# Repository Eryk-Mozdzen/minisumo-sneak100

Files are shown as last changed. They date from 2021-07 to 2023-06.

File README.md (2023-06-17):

# Autonomous minisumo robot Sneak100 

<p align="center">
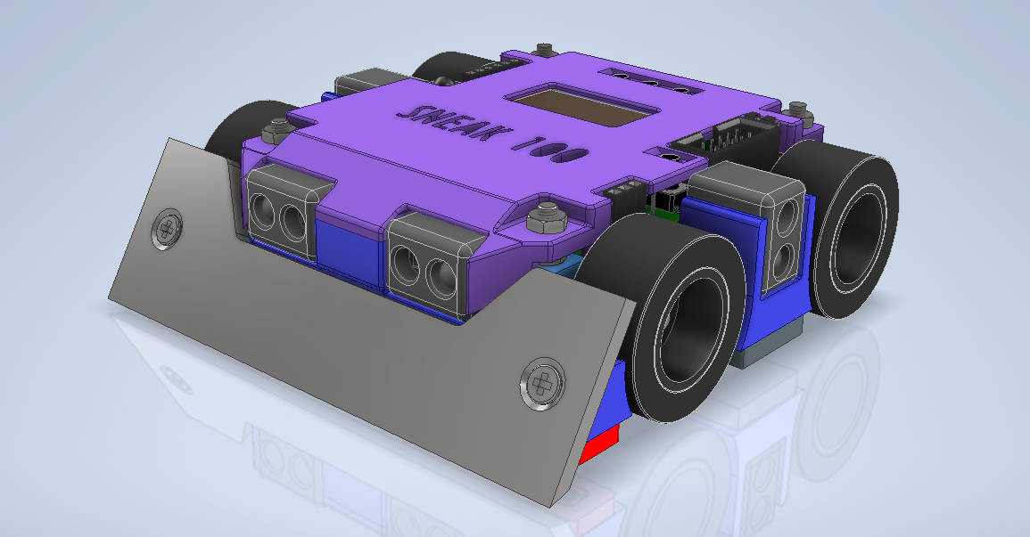
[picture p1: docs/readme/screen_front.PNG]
  
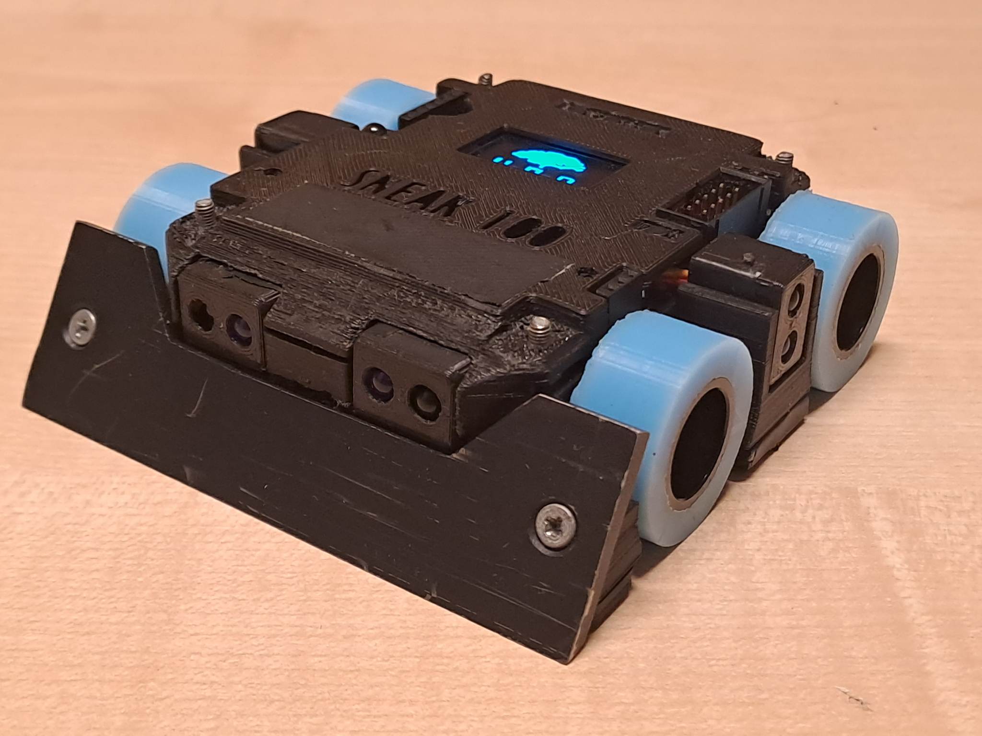
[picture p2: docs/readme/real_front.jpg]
  
</p>

<p align="center">
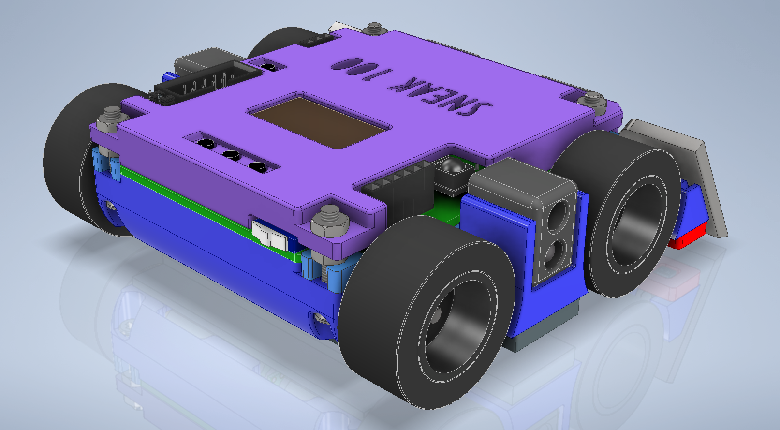
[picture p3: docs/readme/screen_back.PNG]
  
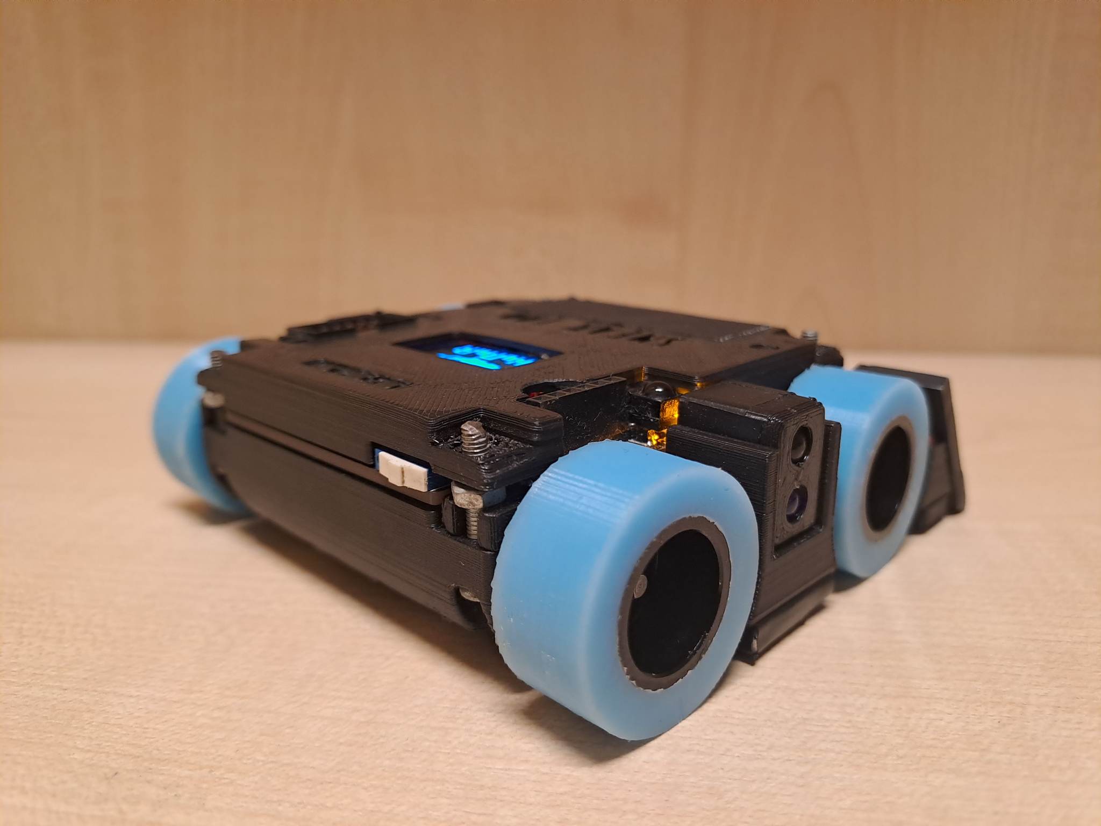
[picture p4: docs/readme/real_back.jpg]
  
</p>

<p align="center">
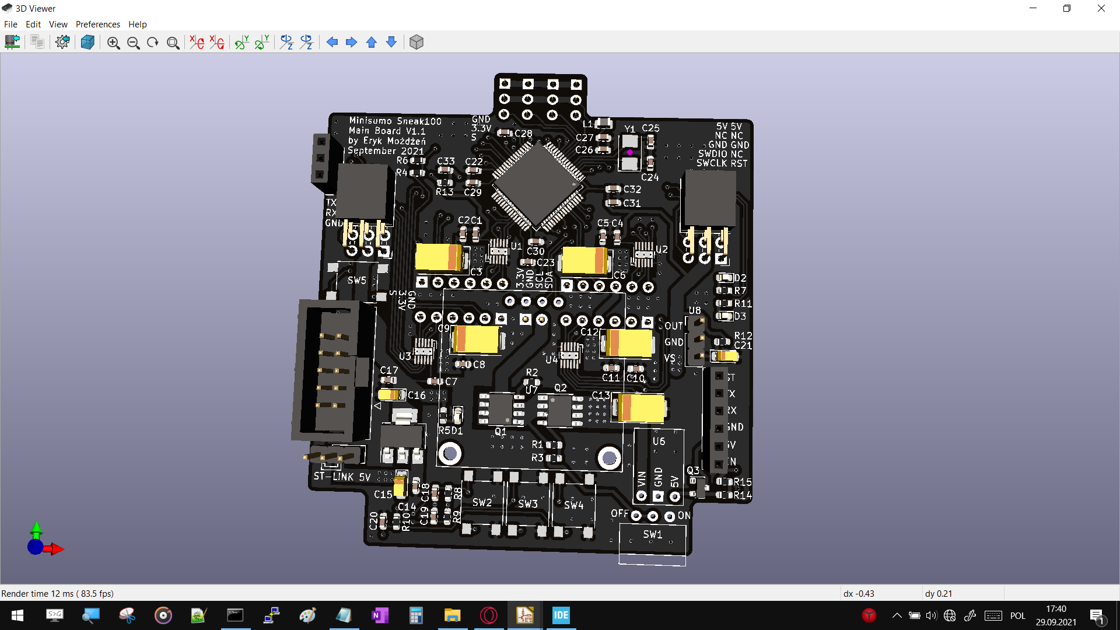
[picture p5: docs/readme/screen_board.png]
  
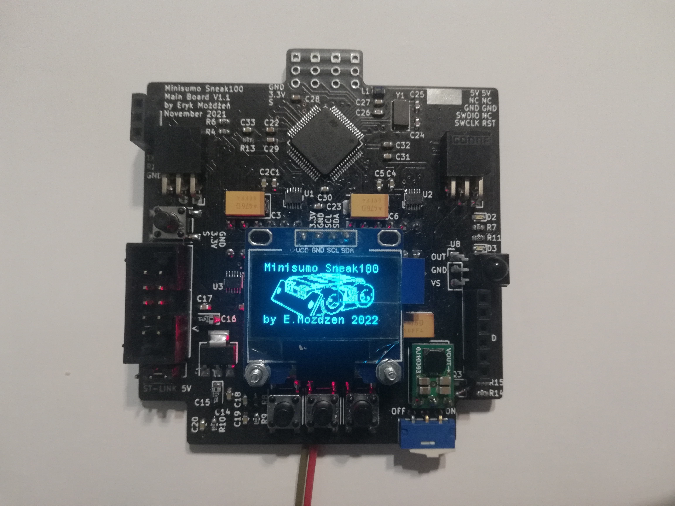
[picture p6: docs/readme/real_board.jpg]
  
</p>

### DEADLINE:
```diff
#  4 sep 2021 - Baltic Robot Battles, Gdansk, Poland (canceled)
- 20 nov 2021 - EastROBO 2021, Bialystok, Poland (missed)
- 28 nov 2021 - ROBOmotion 2021, Rzeszow, Poland (missed)
+  9 apr 2022 - Robotic Tournament, Rybnik, Poland
# 13 may 2022 - Baltic Robot Battles, Gdansk, Poland (canceled)
+ 18 jun 2022 - XIII Robotic Arena, Wroclaw, Poland
-  2 jul 2022 - Drones And Robots Tournament, Krakow, Poland (missed)
+  4 nov 2022 - Robochallnge 2022, Bucharest, Romania
+ 26 nov 2022 - ROBOmotion 2022, Rzeszow, Poland
+  1 apr 2023 - Robotic Tournament, Rybnik, Poland
- 22 apr 2023 - XIV Robotic Arena, Wroclaw, Poland (malfunction)
- 14 may 2023 - Tournoi National de Robotique, Niem, France (malfunction)
```

### Next version:     
- develop spring for blade
- proximity sensors: turn to more front
- hide power switch

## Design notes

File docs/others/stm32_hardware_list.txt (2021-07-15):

proximity sensors:
	- address	3 output
	- tx enable	1 output
	- reflection	1 ADC

line sensors:
	- reflection 	4 ADC

motors:
	- steer		4x2 PWM
	- encoders	4x1 encoder mode

interface:
	- program	SWCLK, SWDIO
	- button	RESET			wycięty
	- user debug	1 UART		zbędny
	- user rc	1 interrupt
	- user button	1 interrupt
	- user leds 	3 output
	
	- IMU		1 SPI/I2C	ok
	- OLED display	1 I2C		ok
	- bluetooth	1 UART		ok
	- start module	2 input		ok	wycięty
	- debug/program	1 USB		ok

others:
	- battery	1 ADC		ok

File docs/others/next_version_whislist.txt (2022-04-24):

version 1.1:
ok	- MOSFET symbol fix
ok	- display mounting holes
ok	- ST-link 5V jumper with 3 pins
ok	- power switch on/off silk layer text
ok	- power led indicator in other place
pass	- swap RC-5 receiver, decoder & state machine to external start module

ok?	- add HC-05 module power control MOSFET
ok	- better STM32 pin usage
ok	- add additional UART
ok	- reset button

version 1.2:
version 2.0:
	- capacitor footprint termo relief
ok	- change polarity of battery input connector to flat side
	- fix proximity sensor connector pinout and add pinout labels / move sensor on the board
ok	- line sensor merged header
ok	- remove HC-05 power control MOSFET / remove HC-05
ok	- add jumper from ST-Link 5V to supply or 5V rail
	- add KoNaR symbol on silk layer
	
	- detachable screen
pass	- detachable 9DOF / 9DOF onboard / 6DOF + 3DOF on board

pass	- use SWO interface for debug, use of real ST-LINK v2, change programming connector to header goldpin

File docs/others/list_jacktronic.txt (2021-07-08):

1	STM32F405RTG6				45	45
6	DRV8835DSSR				5,50	33
5	CD4051 SMD SOP16			1	5
1	Kwarc 8.000 MHz 5x3,2mm 2PAD SMD	3	3
3	Dioda nad.3mm OSIXCA3131A		1,80	5,40
2	Gniazdo USB-mini B smd CANON		2	4

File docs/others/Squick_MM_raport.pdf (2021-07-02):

Projekt

Roboty Mobilne

# Dokumentacja

# Robot mobilny typu MicroMouse

# „Squick”

Skład grupy:
Piotr Gorzelnik, 248947
Patryk Szydlik, 248949

Termin: środa 18:00

Prowadzący:
mgr inż. Arkadiusz Mielczarek

1 lipca 2021

## Spis treści

1 Opis projektu | 2
2 Założenia Projektowe | 2
3 Konfiguracja mikrokontrolera | 3
4 Urządzenia zewnętrzne | 8
5 Projekt elektroniki | 10
6 Konstrukcja mechaniczna | 11
7 Opis działania programu | 14
8 Napotkane problemy | 20
9 Zadania niezrealizowane | 20
10 Podsumowanie | 21
11 Odnośniki do repozytorium GIT Bitbucket | 21

## 1 Opis projektu

Tworzonym przez nas projektem jest robot mobilny klasy micromouse. Będzie on wyposażony w dwukołowy napęd różnicowy (robot mobilny klasy 2.0). Robot będzie korzystał z fuzji czujników odbiciowych time-of-flight oraz czujników stworzonych z nadajników IR oraz fototranzystorów w celu optymalnego rozpoznawania przeszkód (ścian labiryntu). Do orientacji w labiryncie robot będzie wykorzystywać enkodery oraz IMU. Oprócz trybu autonomicznego, robotem będzie także można sterować zdalnie przy użyciu prostej aplikacji mobilnej. Projekt planujemy w przyszłości wykorzystać do wystartowania w zawodach robotycznych. Założenia konstrukcyjne oraz funkcjonalność robota zostały stworzone w oparciu o regulamin konkurencji Micromouse 16x16 odbywającej się na międzynarodowych zawodach robotycznych Robotic Arena.

## 2 Założenia Projektowe

- Użycie mikrokontrolera z rodziny STM32F4
- Stworzenie fuzji dalmierzy laserowych VL oraz ręcznie robionych czujników
- Wykorzystanie enkoderów oraz regulatora PID do sterowania prędkościami silników
- Wykorzystanie IMU oraz modułu Bluetooth
- Pozycjonowanie się w centrum korytarza labiryntu przez regulator PID z czujników odległości
- Obsługa interfejsów komunikacyjnych I2C, SPI, UART
- Konstrukcja mieszcząca się w kwadracie o boku 100mm
- Nisko położony środek ciężkości

### 2.1 Elementy do stworzenia konstrukcji robota

- Mikrokontroler STM32F411RET6 w obudowie LQFP 64 (https://kamami.pl/stm32f4/233364-stm32f411ret6.html?search_query=STM32F4&results=100)
- Czujnik odległości time of flight VL53L0X (https://botland.com.pl/czujniki-swiatla-i-koloru/7176-vl53l0x-time-of-flight-czujnik-odleglosci-i-swiatla-otoczenia-i2c-pololu-2490.html)
- Enkodery magnetyczne do silników pololu micro (https://botland.com.pl/enkodery/4884-zestaw-enkoderow-magnetycznych-do-micro-silnikow-pololu-kompatybilne-z-hpcb-27-18v-2-szt-pololu-3081.html)
- Silniki Pololi HPCB 50:1 z obustronnym wałem (https://botland.com.pl/silniki-dc-micro-z-przekladnia/5093-silnik-hpcb-501-obustronny-wal-pololu-3073.html)
- Moduł komunikacji BT (https://botland.com.pl/moduly-bluetooth/9515-modul-bluetooth-40-ble-hm-10-mlt-bt05-33v5v.html)
- LSM9DS1 - 9DoF IMU - 3-osiowy akcelerometr, magnetometr i żyroskop (https://botland.com.pl/czujniki-9dof-imu/17201-lsm9ds1-9dof-imu-3-osiowy-akcelerometr-magnetometr-i-zyroskop-i2cspi-adafruit-4634.html)
- Nadajniki IR (https://botland.com.pl/diody-ir-podczerwone/279-nadajnik-ir-sfh4550-5mm-850nm.html) oraz Fototranzystory (https://botland.com.pl/fototranzystory/4245-fototranzystor-sfh-313fa-5mm-870nm-5-szt.html)
- Dodatkowe przyciski i przełączniki dla użytkownika
- Diody LED do sygnalizacji
- Multiplekser (http://electropark.pl/4xxx/11374-cd4051-multiplexer-demultiplexer-so16.html)

### 2.2 Możliwości rozwoju konstrukcji w przyszłości

- Wykorzystanie systemu FreeRToS
- Opracowanie filtr Kalmana z IMU
- Wykorzystanie MicroPython-a na mikrokontrolerze
- Wykorzystanie w pełni możliwości FPU na STM32F4
- Rozwinięcie algorytmów eksploracji labirytnu
- Rozwinięcie algorytmów odnajdywania najkrótszej ścieżki

## 3 Konfiguracja mikrokontrolera

Do projektu wybrano mikrokontroler STM32F411RET6 w obudowie LQFP64. Wybór podyktowany został tym, że posiada on wystarczającą moc obliczeniową, ilość potrzebnych peryferiów oraz pamieć flash. Dodatkowo ważnym aspektem była kompatybilność mikrokontrolera z systemami FreeRTOS oraz MicroPython.Na zdjęciu poniżej umieszczono wstępną konfigurację pinów kontrolera, ostateczna struktura może ulec zmianie.

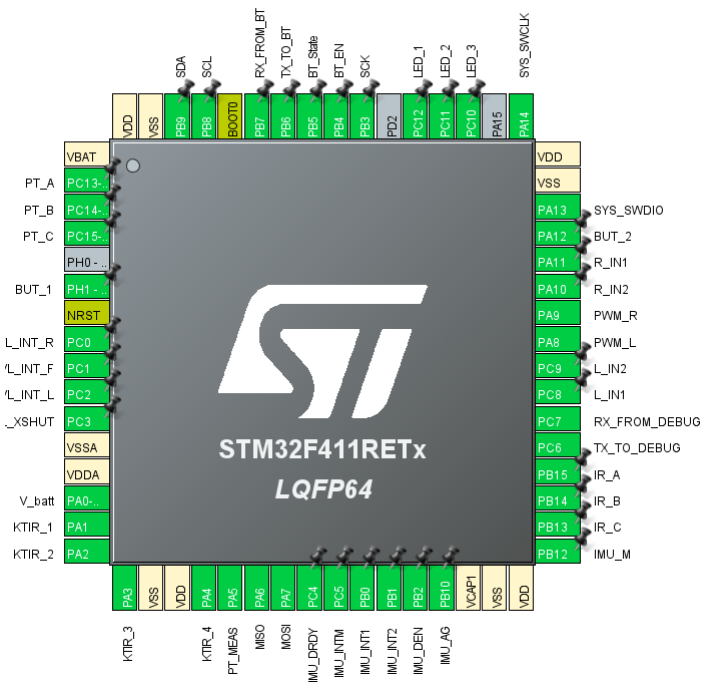
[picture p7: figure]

Rysunek 1: Konfiguracja wyjść mikrokontrolera w programie STM32CubeMX

Rysunek 2: Konfiguracja zegarów mikrokontrolera

### 3.1 Konfiguracja pinów

Numer pinu | PIN | Tryb pracy | Funkcja/etykieta
2 | PC13 | GPIO_Output | PT_A
3 | PC14 | GPIO_Output | PT_B
4 | PC15 | GPIO_Output | PT_C
6 | PH1 | GPIO_Input | BUT_1
8 | PC0 | GPIO_EXTI0 | VL_INT_R
9 | PC1 | GPIO_EXTI1 | VL_INT_F
10 | PC2 | GPIO_EXTI2 | VL_INT_L
11 | PC3 | GPIO_Output | VL_XSHUT
14 | PA0 | ADC1_IN0 | V_batt
15 | PA1 | ADC1_IN1 | KTIR_1
16 | PA2 | ADC1_IN2 | KTIR_2
17 | PA3 | ADC1_IN3 | KTIR_3
20 | PA4 | ADC1_IN4 | KTIR_4
21 | PA5 | ADC1_IN5 | PT_MEAS
22 | PA6 | SPI1_MISO | MISO
23 | PA7 | SPI1_MOSI | MOSI
24 | PC4 | GPIO_Input | IMU_DDRDY
25 | PC5 | GPIO_Input | IMU_INTM
26 | PB0 | GPIO_Input | IMU_INT1
27 | PB1 | GPIO_Input | IMU_INT2
28 | PB2 | GPIO_Output | IMU_DEN
29 | PB10 | GPIO_Output | IMU_AG
33 | PB12 | GPIO_Output | IMU_M
34 | PB13 | GPIO_Output | IR_C
35 | PB14 | GPIO_Output | IR_B
36 | PB15 | GPIO_Output | IR_A
37 | PC6 | USART6_TX | TX_TO_DEBUG
38 | PC7 | USART6_RX | RX_FROM_DEBUG
39 | PC8 | GPIO_Output | L_IN1
40 | PC9 | GPIO_Output | L_IN2
41 | PA8 | TIM1_CH1 (PWM) | PWM_L
42 | PA9 | TIM1_CH2 (PWM) | PWM_R
43 | PA10 | GPIO_Output | R_IN2
44 | PA11 | GPIO_Output | R_IN1
45 | PA12 | GPIO_Input | BUT_2
46 | PA13 | SYS_SWDIO | SYS_SWDIO
49 | PA14 | SYS_SWCLK | SYS_SWCLK
51 | PC10 | GPIO_Output | LED_3
52 | PC11 | GPIO_Output | LED_2
53 | PC12 | GPIO_Output | LED_1
55 | PB3 | SPI1_SCK | SCK
56 | PB4 | GPIO_Output | BT_EN
57 | PB5 | GPIO_Input | BT_State
58 | PB6 | USART1_TX | TX_TO_BT
59 | PB7 | USART1_RX | RX_FROM_BT
61 | PB8 | I2C1_SCL | SCL
62 | PB8 | I2C1_SDA | SDA

Tabela 1: Konfiguracja pinów mikrokontrolera

### 3.2 USART1

Wykorzystany do komunikacji z modułem Bluetooth.

Parametr | Wartość
Baud Rate | 11520
Word Length | 8 Bits (including parity)
Parity | None
Stop Bits | 1
Data Direction | Receive and Transmit
Over sampling | 16 Samples

Tabela 2: Konfiguracja peryferium USART1

### 3.3 USART6

Dodatkowy interfejs UART do komunikacji z osobnym debugerem.

Parametr | Wartość
Baud Rate | 11520
Word Length | 8 Bits (including parity)
Parity | None
Stop Bits | 1
Data Direction | Receive and Transmit
Over sampling | 16 Samples

Tabela 3: Konfiguracja peryferium USART6

### 3.4 I2C1

Interfejs I2C do komunikacji z czujnikami VL

Parametr | Wartość
I2C Speed Mode | Standard Mode
I2C Clock Speed (Hz) | 100 000
Clock No Stretch Mode | Disabled
Primary Address Length selection | 7-bit
Dual Address Acknowledged | Disabled
Primary Slave Address | 0
General Call Address detection | Disabled

Tabela 4: Konfiguracja peryferium I2C1

### 3.5 SPI1

Interfejs SPI do komunikacji z czujnikiem IMU (akcelerometr, żyroskop, magnetometr)

Parametr | Wartość
Frame Format | Motorola
Data Size | 8 Bits
First Bit | MSB First
Prescaler | 16
Baud Rate | 3 MBits/s
Clock Polarity | Low
Clock Phase | 1 Edge
CRC Calculation | Disabled
NSS Signal Type | Software

Tabela 5: Konfiguracja peryferium SPI1

### 3.6 TIM1

To peryferium jest wykorzystywane do zadawania sygnału PWM na silniki

Parametr | Wartość
I2C Speed Mode | Standard Mode
Prescaler | 4
Counter Mode | Up
Counter Period | 999
Internal Clock Division | No Division
Master/Slave Mode | Disable (Trigger input effect not delayed)
Trigger Event Selection | Reset (UG bit from TIMx_EGR)
PWM Generation Channel 1:
Mode | PWM mode1
Pulse | 0
Fast Mode | Disable
CH Polarity | High
PWM Generation Channel 2:
Mode | PWM mode1
Pulse | 0
Fast Mode | Disable
CH Polarity | High

Tabela 6: Konfiguracja peryferium TIM1

### 3.7 TIM2

Ten Timer służy do wywoływania przerwań z częstotliwością 50Hz

Parametr | Wartość
I2C Speed Mode | Standard Mode
Prescaler | 96
Counter Mode | Up
Counter Period | 9999
Internal Clock Division | No Division
Auto-reload Preload | No Disable
Master/Slave Mode | Disable (Trigger input effect not delayed)
Trigger Event Selection | Reset (UG bit from TIMx_EGR)

Tabela 7: Konfiguracja peryferium TIM2

## 4 Urządzenia zewnętrzne

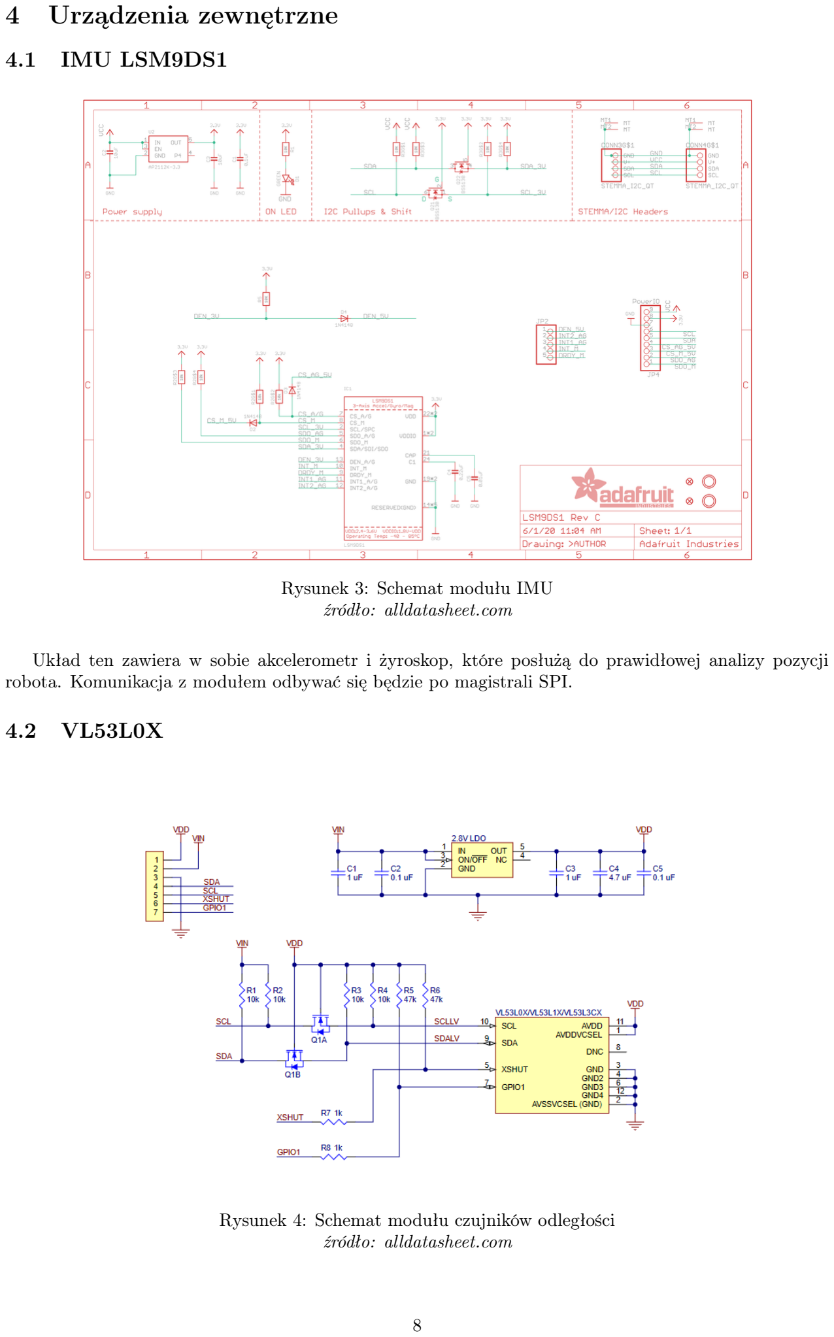
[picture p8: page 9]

### 4.1 IMU LSM9DS1

Rysunek 3: Schemat modułu IMU źródło: alldatasheet.com (https://html.alldatasheet.com/html-pdf/1242998/STMICROELECTRONICS/LSM9DS1/2267/1/LSM9DS1.html)

Układ ten zawiera w sobie akcelerometr i żyroskop, które posłużą do prawidłowej analizy pozycji robota. Komunikacja z modułem odbywać się będzie po magistrali SPI.

### 4.2 VL53L0X

Rysunek 4: Schemat modułu czujników odległości źródło: alldatasheet.com (https://html.alldatasheet.com/html-pdf/948120/STMICROELECTRONICS/VL53L0X/1944/1/VL53L0X.html)

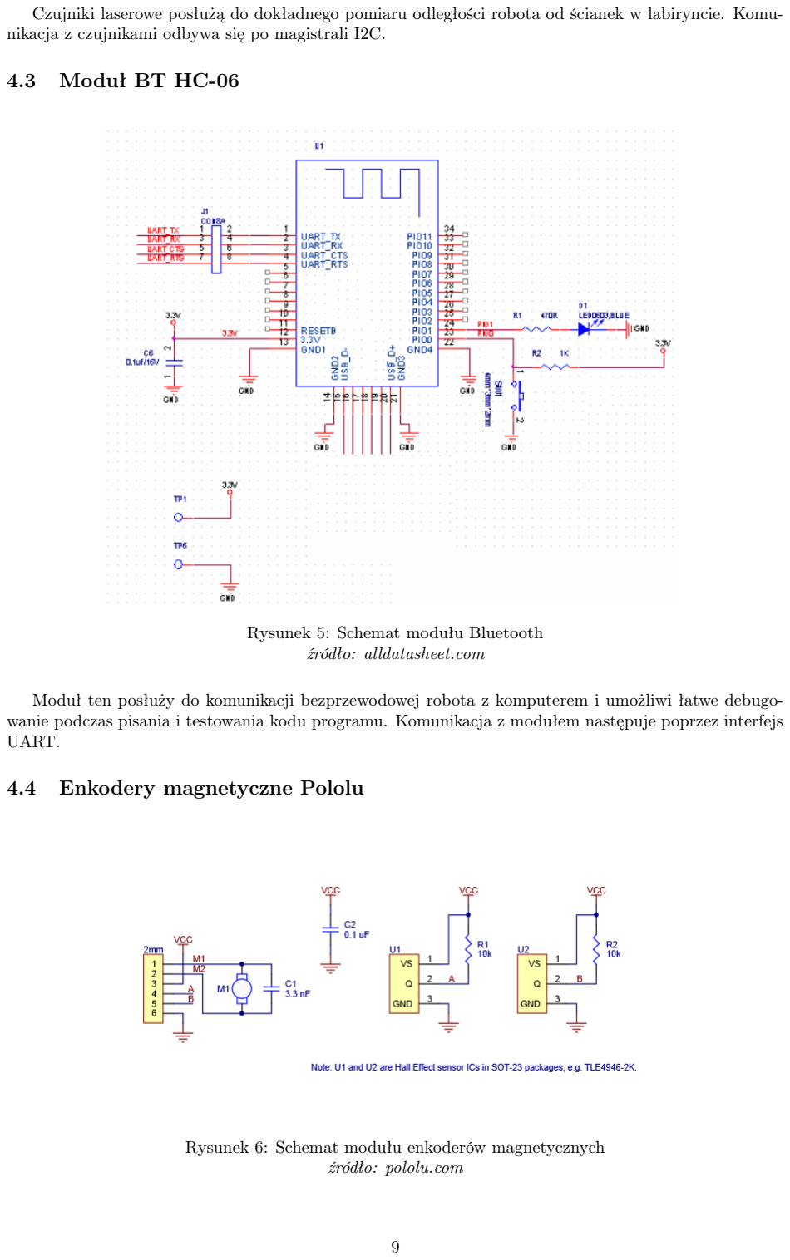
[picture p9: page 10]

Czujniki laserowe posłużą do dokładnego pomiaru odległości robota od ścianek w labiryncie. Komunikacja z czujnikami odbywa się po magistrali I2C.

### 4.3 Moduł BT HC-06

Rysunek 5: Schemat modułu Bluetooth źródło: alldatasheet.com (https://pdf1.alldatasheet.com/datasheet-pdf/view/1179032/ETC1/HC-06.html)

Moduł ten posłuży do komunikacji bezprzewodowej robota z komputerem i umożliwi łatwe debugowanie podczas pisania i testowania kodu programu. Komunikacja z modułem następuje poprzez interfejs UART.

### 4.4 Enkodery magnetyczne Pololu

Rysunek 6: Schemat modułu enkoderów magnetycznych źródło: pololu.com (https://www.pololu.com/file/download/magnetic-encoder-kit-for-micro-metal-gearmotors-schematic.pdf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)

Enkodery magnetyczne wykorzystane zostaną do pomiaru prędkości oraz pozycji obrotowej kół. Zamocowane są one do przedłużonego wału silnika Pololu HCPCB.

## 5 Projekt elektroniki

Schemat całej elektroniki robota znajduje się w załączniku do tego raportu (str. 21). Zarówno schemat elektroniki jak i projekt PCB wykonaliśmy w programie KiCad. Ponieważ płytka drukowana będzie jednocześnie pełnić rolę podwozia, staraliśmy się w miarę możliwości zrobić ją jak najmniejszą, aby zmaksymalizować manewrowalność robota w labiryncie. Z tego też powodu płytka jest dwuwarstwowa.

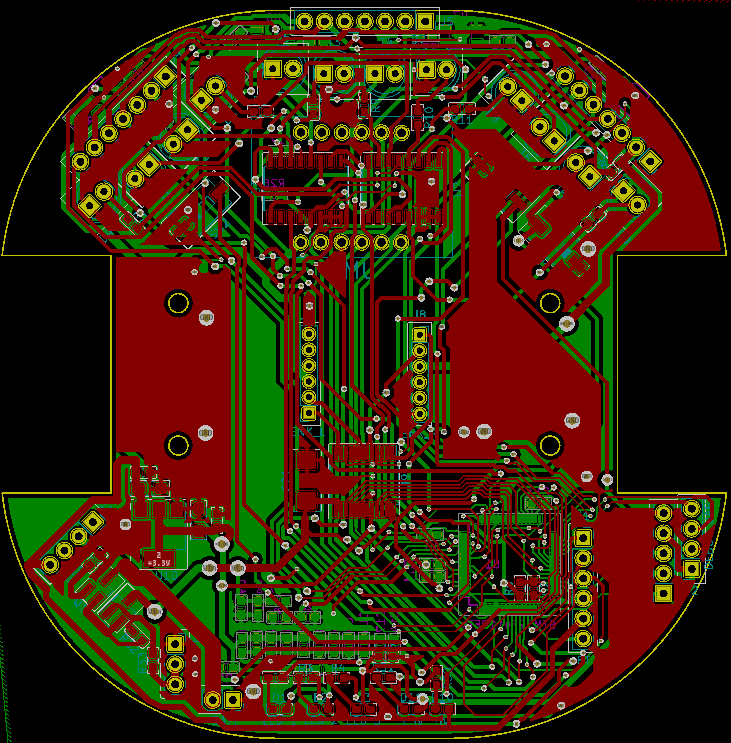
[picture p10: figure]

((a)) Górna warstwa płytki | ((b)) Dolna warstwa płytki

Zdecydowaliśmy się zlecić produkcję płytki w zewnętrznej firmie, aby uniknąć niedoskonałości jakie powstają przy ręcznym wytrawianiu a budżet pozwalał nam na taką wygodę. Zamówienie już do nas dotarło i przewidujemy, że do końca kwietnia ukończymy konstrukcję robota. Poniżej znajdują się zdjęcia gotowych, niepolutowanych płytek.

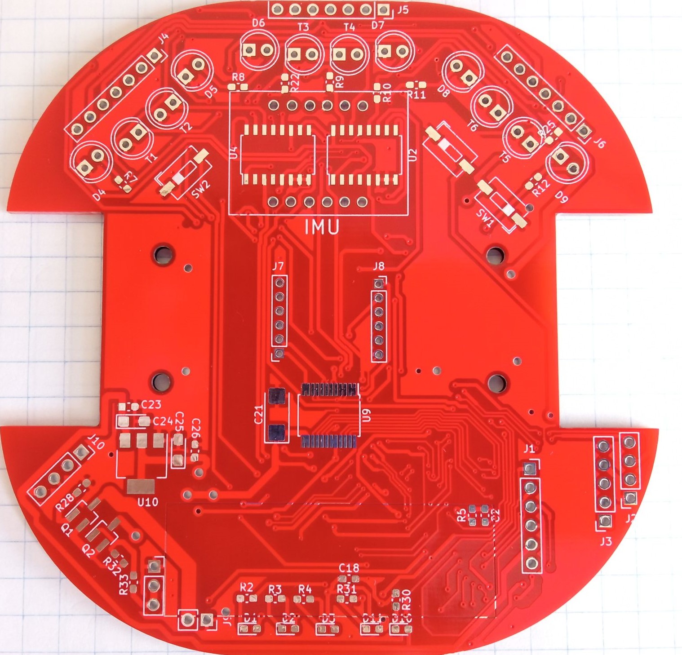
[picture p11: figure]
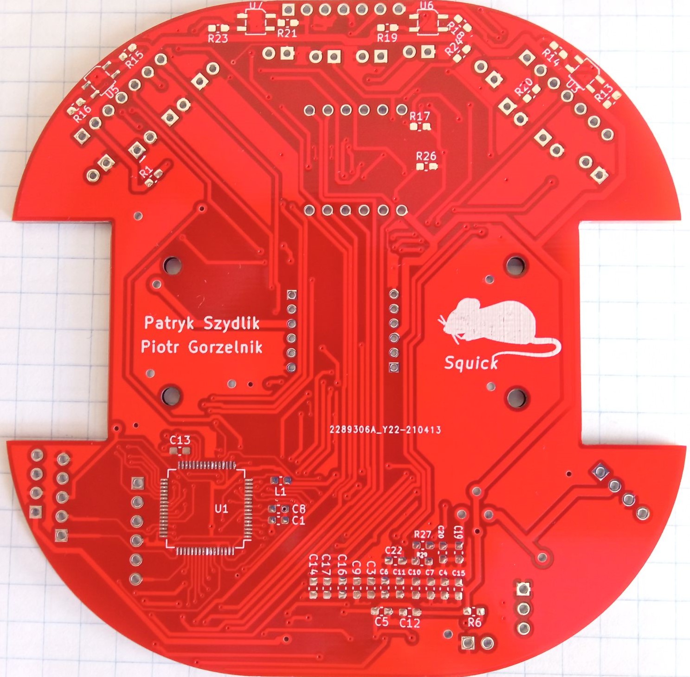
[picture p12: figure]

((a)) Górna warstwa płytki | ((b)) Dolna warstwa płytki

## 6 Konstrukcja mechaniczna

### 6.1 Model 3D

Trójwymiarowy model robota powstał w programie AutoCAD Inventor.

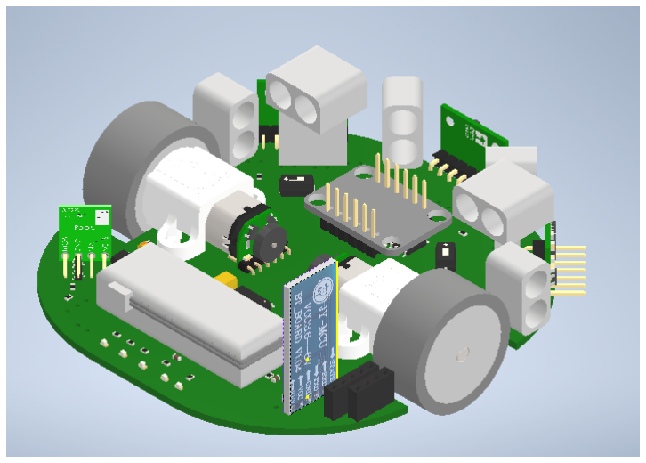
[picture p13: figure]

Rysunek 7: Model konstrukcji robota

Rysunek 8: Rzut z góry modelu robota

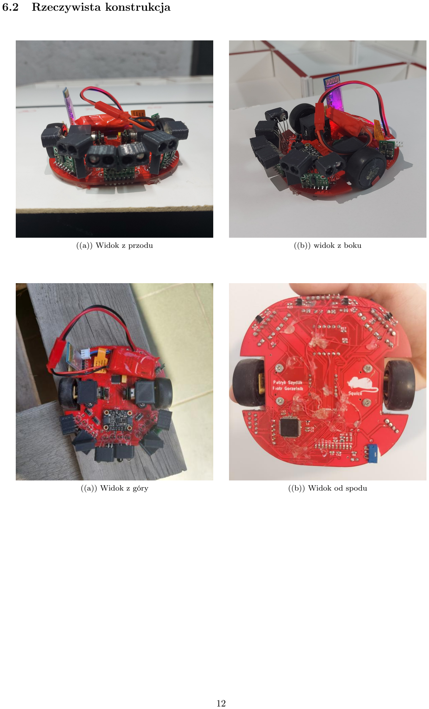
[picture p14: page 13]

### 6.2 Rzeczywista konstrukcja

((a)) Widok z przodu | ((b)) widok z boku
((a)) Widok z góry | ((b)) Widok od spodu

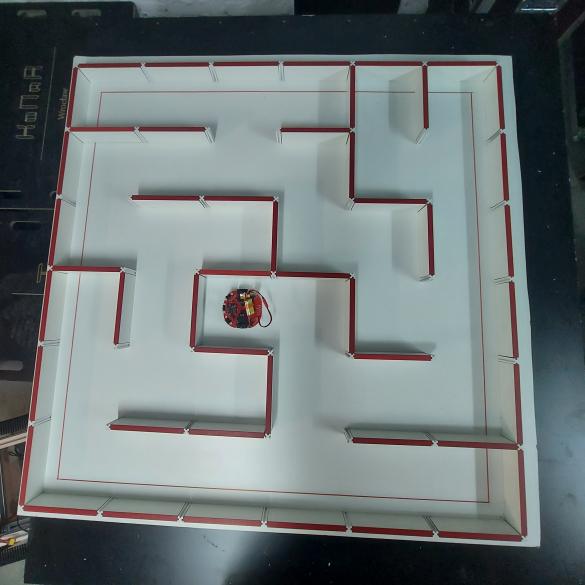
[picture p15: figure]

Rysunek 9: Robot w labiryncie

Jak widać na powyższych zdjęciach, zgodnie z początkowymi założeniami udało nam się stworzyć konstrukcję robota o rozmiarach i kształcie pozwalających na swobodne poruszanie się wewnątrz labiryntu.

## 7 Opis działania programu

### 7.1 Rdzeń programu

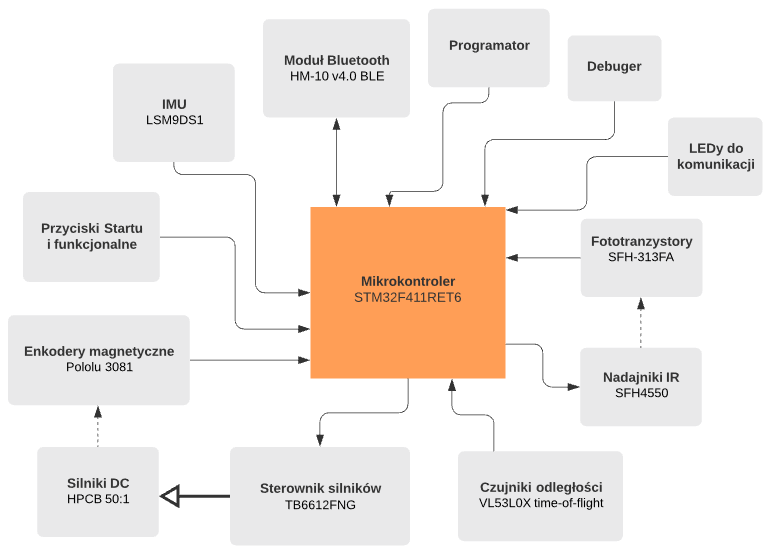
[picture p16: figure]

Rysunek 10: Diagram blokowy rdzenia programu

### 7.2 Obsługa czujników i sterowników

### 7.2.1 Obsługa enkoderów

Po podłączeniu prawidłowym enkoderów Pololu oraz dodatkowym skonfigurowaniu wyjść TIM3 CH1 CH2 oraz TIM2 CH1 CH2 jako encoder mode możliwy był odczyt impulsów odbieranych przez enkodery, a następnie prawidłowa ich konwersja na jednostki odległości mierzone w mm.

Pierwszym ważnym etapem konwersji było skalibrowanie pomiarów z enkoderów oraz ich prawidłowa konwersja:

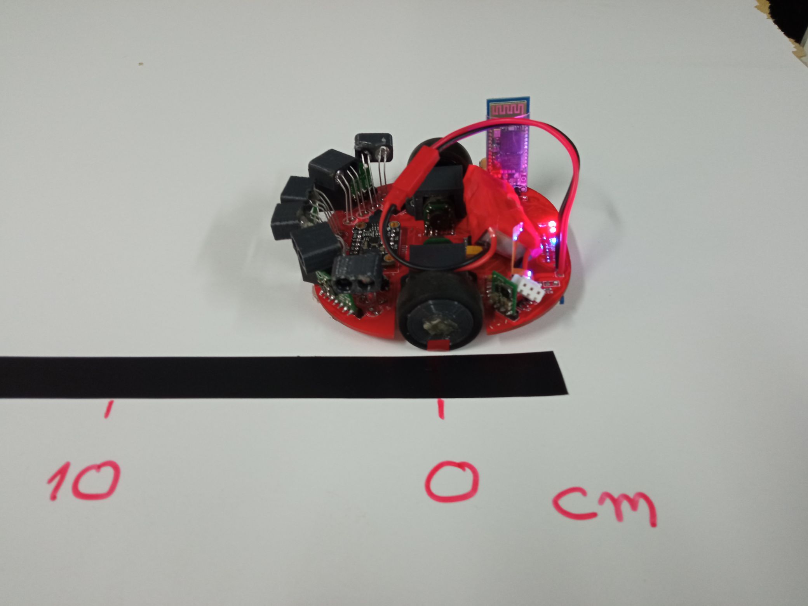
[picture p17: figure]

((a)) Pozycja startowa | ((b)) Wartości odczytów z enkoderów

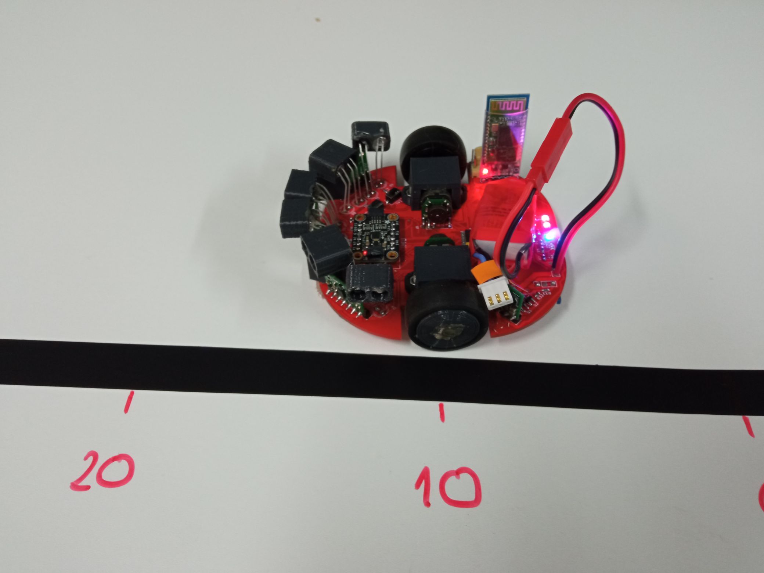
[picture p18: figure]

((a)) Pozycja po przesunięciu o 10cm | ((b)) Odczyty po przesunieciu

Kolejną istotną kwestią po skalibrowaniu odczytów pozycji robota ważne było aby prawidłowo przekształcać i wykorzystywać odczyty z prędkości. W tym celu wykonany był kolejny odpowiedni pomiar, w którym robot przejeżdżał przez sekundę po torze z zadanym wypełnieniem PWM oraz co 100ms wyświetlał pozycję i prędkość.

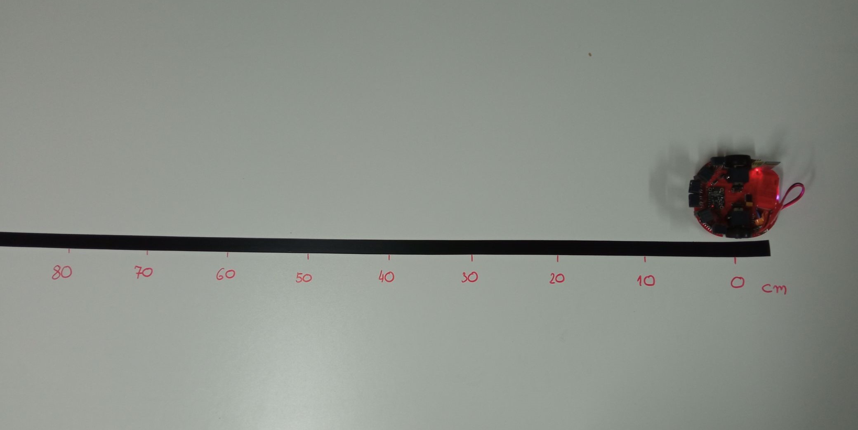
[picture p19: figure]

Rysunek 11: Pozycja startowa na torze

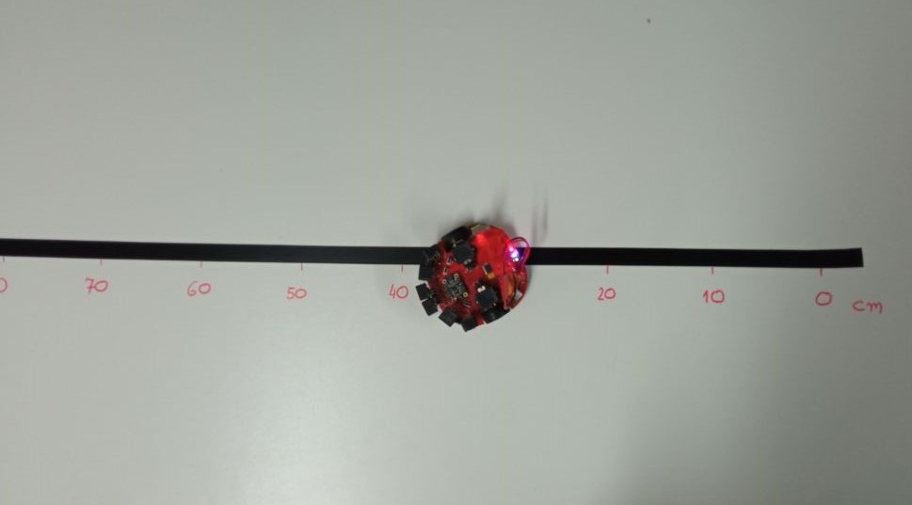
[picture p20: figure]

Rysunek 12: Pozycja końcowa na torze

Rysunek 13: Odczyt z kalibracji

### 7.2.2 Kalibracja PID kontrolującego silniki

Po prawidłowym obsłużeniu odczytów z enkoderów możliwe było napisanie regulatora PID i ręczne jego nastrojenie.
Na poniższych screenach SET oznacza wartość oczekiwaną, MEAS jest wartością zmierzoną na enkoderach, RES to poprawka regulacji PWM wysłanego na silniki.

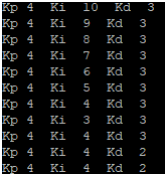
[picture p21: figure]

Rysunek 14: Strojenie PID

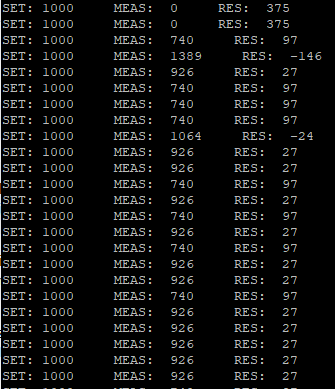
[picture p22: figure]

Rysunek 15: Start regulacji

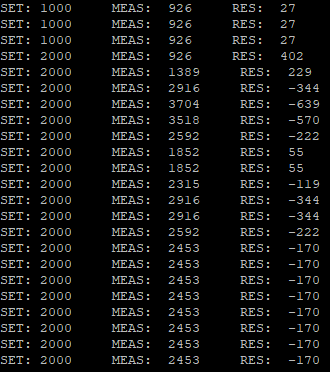
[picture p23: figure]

Rysunek 16: Zmiana set point

Rysunek 17: Wyzerowanie set point

### 7.2.3 Obsługa pomiarów ADC

Odczyty ADC posłużyły m.in do pomiaru i pilnowania stanu napięcia na baterii jak również do oczytów z czujników KTIR, które służą do wykrywania linii na torze.
Niestety jeden z czujników KTIR nadal nie działał. Najprawdopodobniej uszkodzeniu mogły ulec ścieżki prowadzące do tegoż czujnika i nie odbieraliśmy z niego żadnych sygnałów.

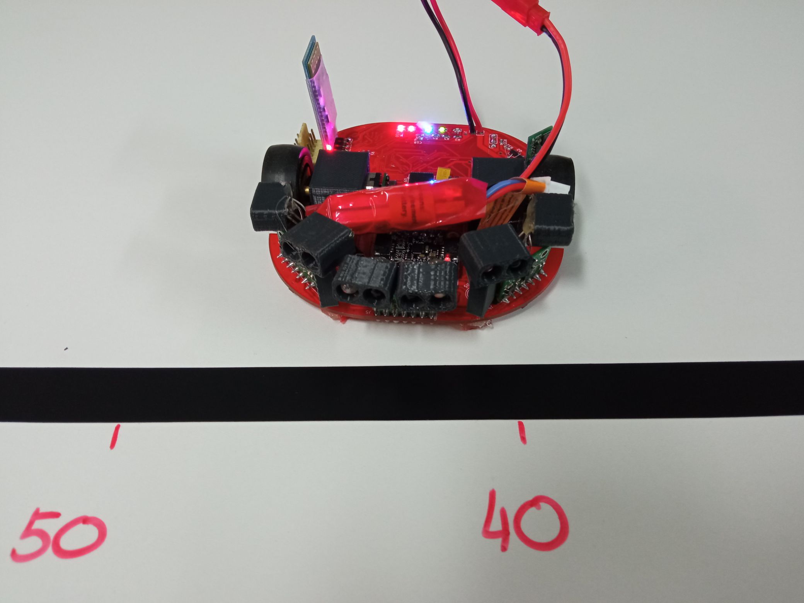
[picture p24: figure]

((a)) Położenie robota | ((b)) Odczyty białej powierzchni

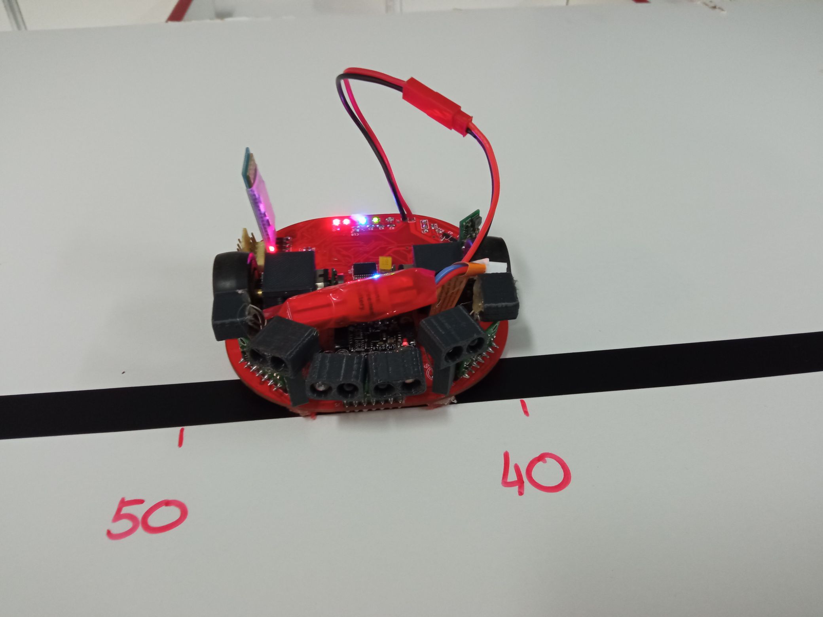
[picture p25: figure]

((a)) Położenie robota nad linią | ((b)) Odczyty czarnej powierzchni

### 7.2.4 Multiplekser i czujnik IR

Niestety popełniliśmy błąd w składaniu i lutowaniu konstrukcji, który spowodował, że przez mieszane opisy nóżek kolektora i emitera w fototranzystorach wszystkie zostały polutowane odwrotnie i odczyty są nieprawidłowe.
Jednakże udało nam się jeszcze przelutować jedną parę czujników aby zademonstrować odczyty z sensora IR.

Rysunek 18: Odczyty z czujnika przy zasłoniętym i odsłoniętym czujniku

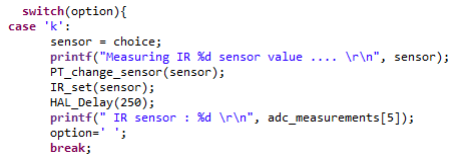
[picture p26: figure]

Rysunek 19: Kod wywołujący pomiar

### 7.3 Opis algorytmu eksploracji labiryntu (w trakcie implementacji)

Robot będzie miał za zadanie dotrzeć w jak najkrótszym czasie z pozycji startowej do docelowej, wykorzystując dwa przejazdy po labiryncie. W pierwszym przejeździe robot mapuje labirynt do momentu odnalezienia celu (środka labiryntu). W drugim przejeździe wybiera najkrótszą drogę z pośród zmapowanych w pierwszym przejeździe komórek. Do odnajdywania najkrótszej drogi od startu (jednego z narożników) do mety (środka) w labiryncie zaimplementujemy w robocie algorytm zalewania (ang. floodfill). Zalewanie rozpoczyna się od miejsca docelowego, czyli środka labiryntu złożonego z czterech kwadratowych komórek. Przed rozpoczęciem pierwszego przejazdu robot nie ma żadnej wiedzy o strukturze labiryntu, dlatego przy pierwszym zalewaniu traktujemy labirynt jako pusty kwadrat o 256 polach - indeksy pól rosną równomiernie we wszystkich kierunkach. Wykorzystanie algorytmu zalewania podczas mapowania i poszukiwania celu powinno spowodować, że robot zacznie szybko zmierzać w kierunku środka labiryntu po wyruszeniu z pola startu.

W czasie eksploracji (pierwszego przejazdu) robot wykrywa ściany komórki, w której aktualnie się znajduję a następnie sprawdza czy istnieje sąsiedni blok o mniejszym lub równym indeksie, do którego może się przemieścić. Zalewanie labiryntu następuję dopiero wtedy, gdy wszystkie dostępne sąsiednie bloki mają większe wartości od wartości bloku, w którym aktualnie znajduje się robot. Ta operacja powoduje zmianę dotychczasowych wartości bloków labiryntu i wyznaczenie nowej trasy prowadzącej do celu (w kierunku malejących wartości). Po osiągnięciu celu następuję ostatnie zalewanie i wyznaczana jest najkrótsza droga łącząca punkt startowy z celem spośród zmapowanej części labiryntu.

Rysunek 20: Diagram algorytmu zalewania

## 8 Napotkane problemy

### 8.1 enkodery

Okazało się, że na etapie projektowania elektroniki i płytki zapomnieliśmy o poprowadzeniu czterech ścieżek z enkoderów do mikrokontrolera. Na szczęście mieliśmy kilka wolnych pinów na mikrokontrolerze, dlatego udało nam się naprawić błąd przy pomocy kynaru i kleju na gorąco (efekt widoczny na zdjęciu dolnej warstwy płytki na str. 12).

### 8.2 czujniki odległości

Wykorzystane przez nas moduły VL53L0X okazały się być dość skomplikowane w obsłudze pomimo dostarczonych przez producenta bibliotek API. Aby ustawić adres jednego takiego czujnika przez I²C, dwa pozostałe muszą być wyłączone. Nie wzięliśmy pod uwagę konieczności przemiennego wyłączania tych czujników w czasie projektowania elektroniki, dlatego wszystkie były połączone do tej samej linii XSHUT. Planowaliśmy odlutować moduły, osobno poustawiać ich adresy i przylutować spowrotem na miejsce. Niestety, adresy restartują się do ustawienia fabrycznego każdorazowo po wyłączeniu zasilania. Problem udało nam się rozwiązać przerywając połączenie z linią XSHUT dwóch modułów i łącząc je za pomocą kynara do dwóch wolnych pinów pozostałych po wcześniejszym module Bluetooth (wymieniliśmy model BT HM-10 na HC-06).

## 9 Zadania niezrealizowane

Udało nam się zrealizować prawie wszystkie założenia projektowe. Wynikło kilka opóźnień z powodu problemów technicznych z konstrukcją robota, na których naprawę musieliśmy postawić priorytet.

### 9.1 Autonomia

Z powodu niedoszacowania czasu potrzebnego na realizację wcześniejszych etapów projektu oraz napotkanych po drodze problemów technicznych, nie udało nam się dokończyć algorytmu eksploracji labiryntu na czas.

### 9.2 Kompletna obsługa czujników odległości

Z obsługą czujników odległości mieliśmy najwięcej problemów. Po wielu próbach zmiany kodu, zwracane przez nie dane nadal nie są na tyle zadowalające, aby możliwe było omijanie przeszkód.

## 10 Podsumowanie

Pomimo napotkania pewnych problemów, znaczną większość z nich rozwiązaliśmy z zadowalającym efektem. Udało nam się skonstruować robota mobilnego klasy 2.0 o satysfakcjonującej konstrukcji mechanicznej i elektronicznej. Robot jest mały, zwrotny i szybki. Po dopracowaniu oprogramowania Squick będzie mógł rywalizować na zawodach robotycznych w kategorii Micromouse z innymi robotami.

## 11 Odnośniki do repozytorium GIT Bitbucket

- Bitbucket Squick CubeIDE (https://bitbucket.org/konar/squick_cubeide/)
- Bitbucket Squick KiCAD (https://bitbucket.org/konar/squick_kicad/src/)
- Bitbucket Squick Documentation (https://bitbucket.org/konar/squick_documentation/src/main/)
- Bitbucket Squick Inventor (https://bitbucket.org/konar/squick_inventor/src/main/)

## Schematy elektroniczne robota klasy Micromouse „Squick”

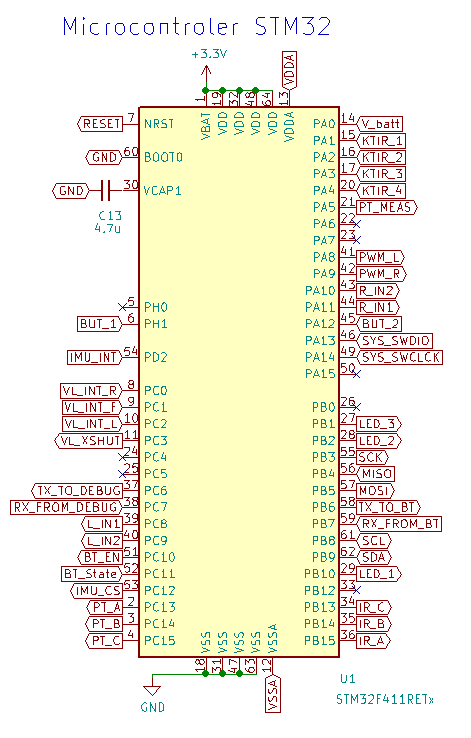
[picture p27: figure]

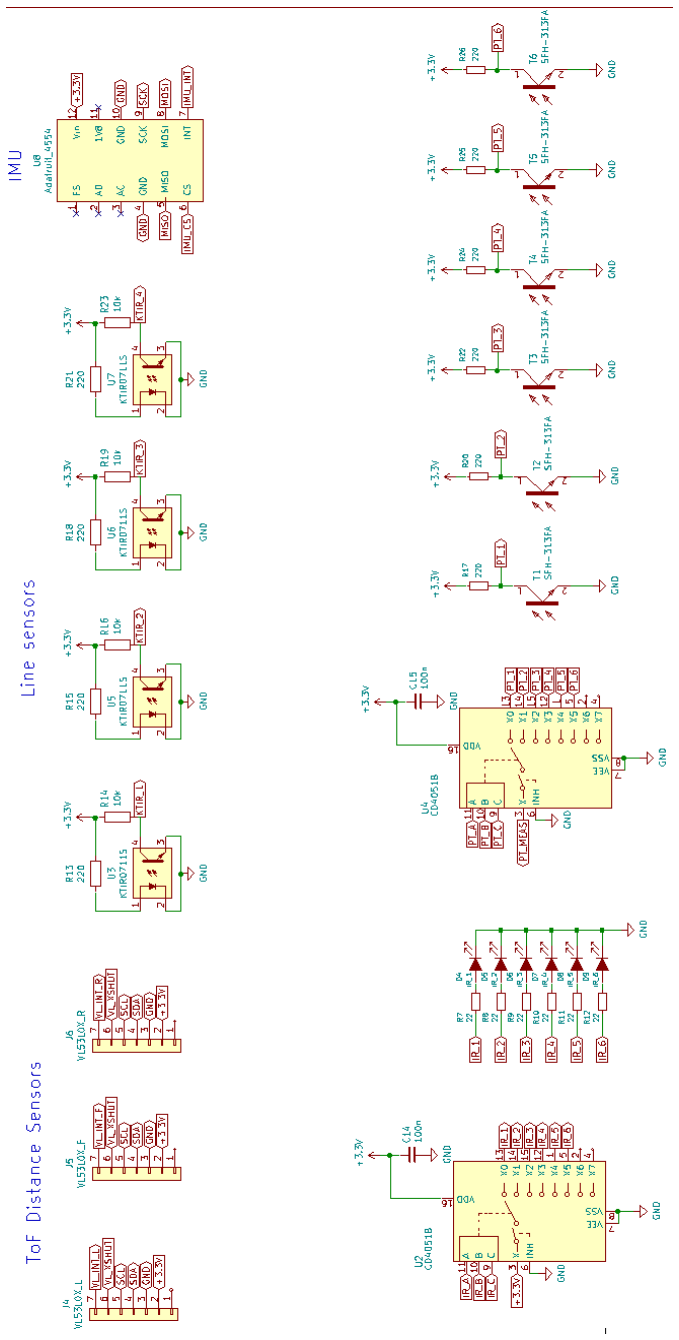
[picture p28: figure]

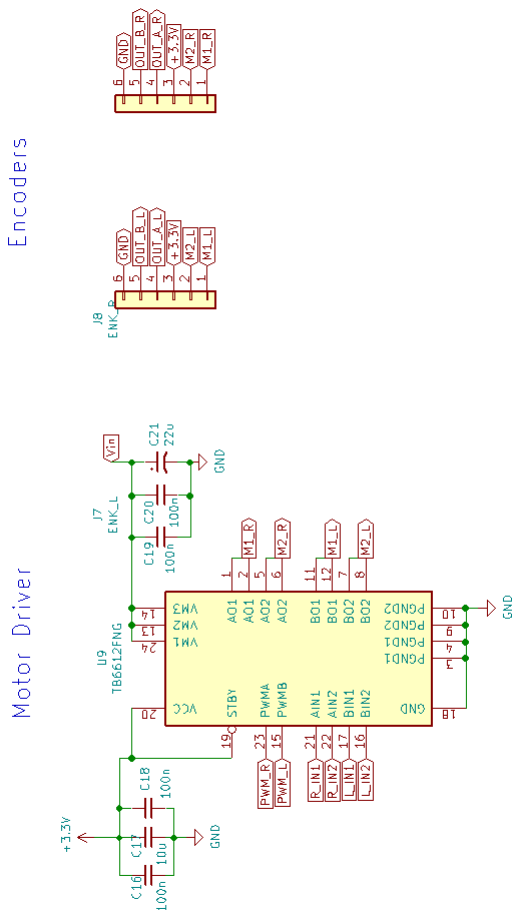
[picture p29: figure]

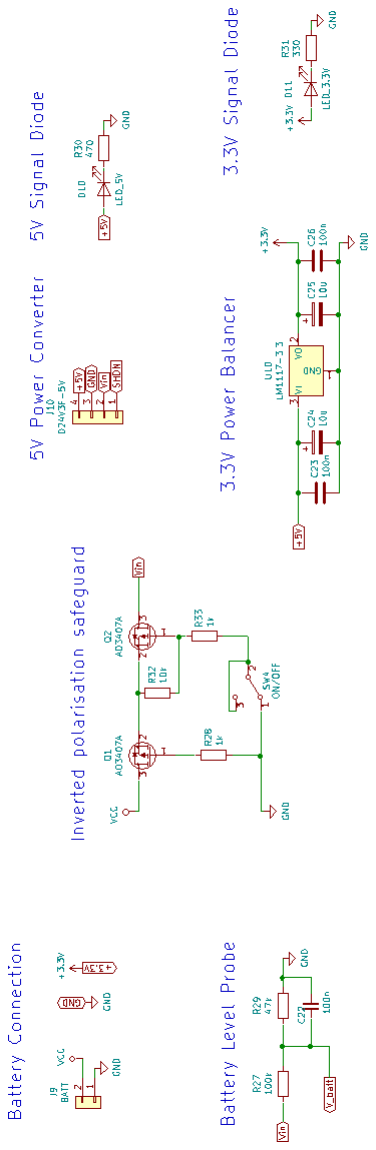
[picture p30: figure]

## Literatura

[1] Marek Galewski. Aplikacje i ćwiczenia w języku C z biblioteką HAL.
Wydawnictwo BTC, Legionowo, Lipiec 2019.
[2] Jan Kędzierski. Filtr Kalmana - zastosowania w prostych układach sensorycznych.
Wrocław, Październik 2007.
[3] Dawid Perdek. Badanie własności algorytmów poszukiwania ścieżki w labiryncie dla robota klasy micromouse.
Wrocław, Grudzień 2015.
[4] STMicroelectronics. STM32F411RET6 datasheet. 2014
[5] STMicroelectronics. VL53L0X datasheet. 2016
[6] STMicroelectronics. LSM9DS1 datasheet. 2015

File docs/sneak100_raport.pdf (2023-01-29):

# Dokumentacja

# Robot mobilny klasy minisumo „Sneak100”


# Eryk Możdżeń

## 2 Września 2022

## Spis treści

1 Wstęp | 2
2 Założenia projektowe | 2
3 Mechanika | 2
4 Elektronika | 9
5 Program | 14
6 Zdjęcia | 16
7 Podsumowanie | 17
8 Odnośnik do repozytorium GIT | 17

## 1 Wstęp

W niniejszym dokumencie zostały zawarte informacje na temat budowy oraz działania robota „Sneak100”. Wyodrębnienie tego projektu spośród innych nastąpiło po powrocie z zawodów ”XII Robotic Arena” w styczniu 2020 roku, na których skrystalizowała się wizja 4-kołowego, niskiego robota minisumo.

## 2 Założenia projektowe

- Działanie w pełni autonomiczne
- Użycie mikrokontrolera z rodziny STM32F4
- Zastosowanie 4 odrębnie napędzanych kół
- Wszystkie koła sterowane w zamkniętej pętli z użyciem enkoderów inkrementalnych
- Użycie więcej niż 2 odbiciowych czujników linii
- Zastosowanie w roli czujników wykrycia przeciwnika par: dioda nadawacza + fototranzystor
- Użycie maksymalnie dużej ilości czujników wykrycia przeciwnika
- Zastosowanie odbiornika podczerwieni do emulowania modułu startowego
- Konstrukcja możliwie niska
- Konstrukcja o obrysie mieszczącym się w polu 100x100mm
- Waga nieprzekraczająca 500g

## 3 Mechanika

### 3.1 Iteracje projektu

Początkowo projekt zakładał zastosowanie jednej płytki PCB w okolicach podwozia konstrukcji w którą na stałe miały być wlutowane wyprowadzenia silników, enkoderów, odbiciowe czujniki linii oraz czujniki wykrycia przeciwnika, aby zminimalizować ilość przewodów (jeden element elektroniczny konstrukcji). Pomysł ten został w końcu porzucony z uwagi na brak wystarczającego miejsca na płytce.

(a) wersja koncepcyjna Alpha, czerwone opony, czarny kadłub, nóż u dołu duża inspiracja robotem Flash [3]


(b) wersja koncepcyjna Beta, ruchoma głowica z pługiem i czujnikami
(c) wersja koncepcyjna Gamma, wyższa konstrukcja, pług przykręcany od przodu
(d) wersja koncepcyjna Delta, ”przymiarka” docelowej baterii

Rysunek 1: Ewolucja projektu, wersje koncepcyjne, program Autodesk Inventor 2021

### 3.2 Projekt mechaniki

Ostatecznie, projekt zatracił właściwość jazdy po obu stronach, czyli po wywróceniu staje się bezbronny. W najwyższym punkcie konstrukcja osiąga niecałe 32mm ponad płaszczyznę poruszania się. Zaokrąglone ścięcie w tylnej części kadłuba zapewnia stały kontakt tylnich kół z podłożem, nawet podczas znacznego uniesienia frontu pojazdu. W roli pługu został zastosowany nóż do strugarek ze stali narzędziowej z ostrzem z węglika spiekanego, w którym wykonano wycięcie na przednie czujniki wykrycia przeciwnika.
Główna płytka PCB jest umieszczona ponad baterią i silnikami, tak jak w robocie DevexDestroyerDroid [4]. Umożliwiło to wmontowanie ekranu OLED prosto w płytkę drukowaną.


(a) widok pod skosem z przodu, obecny moduł Bluetooth HC-05
(b) widok pod skosem z tyłu, obecny moduł Bluetooth HC-05
(c) widok z góry, od lewej:
gniazdo modułu Bluetooth, odbiornik podczerwieni, 3 przyciski ekran OLED, gniazdo programatora
(d) widok z dołu,
widoczna pokrywa baterii oraz odbiciowe czujniki linii


(e) widok z przodu | (f) widok z tyłu, widoczny włącznik


(g) widok z lewej | (h) widok od środka, widoczna bateria, silniki, enkodery, w przedniej części widoczne kanały przewodów czujników linii

Rysunek 2: Model 3D, program Autodesk Inventor 2021,
niebieski - korpus, fioletowy - pokrywa górna, srebrny - pług, czerwony - obudowa czujników linii, szary - ołowiane obciążniki

### 3.3 Dobór przekładni silników oraz baterii

Jednostki napędowe (silniki wraz z przekładniami jako całość) to szeroko stosowane napędy typu Micro High Power (https://botland.com.pl/silniki-dc-micro-z-przekladnia/5092-silnik-hpcb-301-obustronny-wal-pololu-3072-5904422306335.html) firmy Pololu. Został wybrany wariant z karbonowymi szczotkami (HPCB), które zapewniają zwiększoną żywotność i odporność na pracę pod obciążeniem.
Do przeanalizowania dostępnych kombinacji bateria - przekładnia, zostały zamodelowane dwa czynniki: czynnik proporcjonalny do maksymalnej prędkości liniowej robota V oraz czynnik proporcjonalny do siły z jaką robot jest w stanie oddziaływać na przeciwnika M.
Fpush ∝ M = C · R · n | (1)

vmax ∝ V =

C
R

(2)

- C - ilość cel w baterii LiPO (np. dla 2S C = 2)
- R - przełożenie przekładni silnika (np. dla 30:1 R = 30)
- n - ilość kół

Idealny wybór maksymalizował by oba czynniki, jednak jest to niemożliwe. Aby zobrazować możliwe kombinacje, została stworzona tabela, w której punktem odniesienia został robot Scalak [2].

robot | Scalak (2 koła) | Sneak100 (4 koła)
bateria | 3S | 2S | 3S
przekładnia | 50:1 | 50:1 | 30:1 | 50:1 | 30:1
M | 300 (100%) | 400 (+33%) | 240 (-20%) | 600 (+100%) | 360 (+20%)
V | 0.06 (100%) | 0.04 (-33%) | 0.067 (+11%) | 0.06 (+0%) | 0.1 (+67%)

Tablica 1: Tabela doboru przekładni silników kolorem zielonym został zaznaczony wybrany wariant

Jak widać najlepsze rezultaty osiągane są dla baterii 3S, jednak ze względu na swoje rozmiary musiała być wykluczona z dalszych rozważań.
Z uwagi na pierwotne założenia projektu (wysoka mobilność), został wybrany wariant baterii 2S wraz z przekładnią 30:1, który charakteryzował się większą prędkością liniową konstrukcji (robot Scalak czasami wydawał się zbyt powolny). Osłabienie w zwarciu powinno zostać nadrobione wymanwerowaniem przeciwnika.

### 3.4 Wydruki 3D

Pliki STL zostały bezpośrenio zapisane z Autodesk Inventor-a, a kod gcode został wygenerowany w programie Voxelizer 2.0 (dedykowany program producenta dostępnej drukarki). Elementy zostały wydrukowane z czarnego PLA. Kolor został wybrany tak, aby utrudniać wykrycie przez przeciwnika z czujnikami opartymi o światło podczerwone (obecnie większość robotów takich używa).


Rysunek 3: Wszystkie wydruki 3D tworzące konstrukcję robota, od lewej: obudowa górna, cztery obudowy czujników wykrycia przeciwnika, dwie obudowy czujników linii, korpus, dwie belki blokujące silniki

Mocowanie czujników linii

Czujniki odbiciowe w postaci małych modułów zostały zamontowane parami w niewielkich koszykach wymodelowanych tak, aby zakrywały cały czujnik z wyjątkiem głowicy modułu. Całość została przykręcona na pojedynczą śrubę M3 z płaskim łbem.

(a) widok z góry i z dołu, widoczne kwadratowe otwory na czujniki oraz okrągłe na śrubę
(b) czujnik osadzony w gnieździe, czujnik po za gniazdem


(c) widok z dołu z osadzonymi czujnikami, śruba z płaskim łbem ”chowa się” wewnątrz obudowy
(d) widok z przodu, przewody ułożone w kanałach, śruba przykręcona do nakrętki umieszczonej w specjalnym wycięciu

Rysunek 4: Sposób montażu odbiciowych czujników linii

Korpus – mocowanie silników

Silniki zostały osadzone za pomocą specjalnych gniazdach imitujących fabryczne mocowania zastosowanych silników firmy Pololu. W każdym z nich zostało umieszczone odpowiednio wyprofilowane wycięcie, które uniemożliwia ruch przekładni (a wraz z tym silnika) do środka i na zewnątrz pojazdu, co było dużym problemem w robocie Scalak[2].
Belki blokujące zapobiegają wysuwanie się przekładni w górę, a także stanowią podstawę pod płytkę elektroniczną, dzięki czemu powstaje przestrzeń o lepszych zdolnościach chłodzących silnik.
(a) miejsca na przekładnie silników, widoczne wycięcia zapobiegające wysuwaniu się zespołu napędowego w bok
(b) przekładnia silników w pełni osadzona w korpusie


(c) belka blokująca przykręcona na śruby dociska przekładnie do wnętrza wycięcia

Rysunek 5: Sposób osadzania silników w korpusie robota

Czujniki wykrycia przeciwnika

Każdy pojedynczy czujnik wykrycia przeciwnika został zamknięty w obudowie, której głównym zadaniem było odseparowanie nadajnika (podczerwona dioda LED) oraz odbiornika w osobnych przestrzeniach przy jednoczesnym nieograniczaniu możliwości wykrywania obiektów na wprost sensora.
W praktyce przestrzeń wykrywania przypomina stożek, a umiejscowienie czujników w korpusie zapewnia częściowe pokrywanie się tych pól (estymacja położenia przeciwnika jest dzięki temu bardziej dokładna).
(a) porównanie stanu fabrycznego oraz spreparowanego
(b) widok z przodu, pług przykręcony do korpusu„ śruby nie wystają po za płaszczyznę noża

Rysunek 6: Wykonanie i montaż pługu robota

### 3.5 Pług

W roli pługu został użyty nóż typu HM do strugarek. Ostrze zostało wykonane z węglika spiekanego. Za pomocą szlifierki kątowej zostało wykonane podłużne okno dla czujników wykrycia przeciwnika. Całość została pomalowana czarną farbą w spray-u chroniącą przed korozją oraz utrudniającą wykrycie przez przeciwnika.


(a) porównanie stanu fabrycznego oraz spreparowanego
(b) widok z przodu, pług przykręcony do korpusu„ śruby nie wystają po za płaszczyznę noża
(c) widok z dołu, widoczne wycięcie na nakrętkę, podłużny otwór umożliwia delikatną regulację pozycji ostrza noża względem podłoża

Rysunek 7: Wykonanie i montaż pługu robota

### 3.6 Koła

Zostały zakupione popularne koła Solarbotics RW2i o średnicy 29 mm. Docelowo opona zostanie odlana z sylikonu formierskiego, ponieważ fabryczne ogumienie nie posiada wystarczająco dobrej przyczepności do podłoża.


(a) felga oraz gumowa opona | (b) korpus nie wystaje po za obrys opony co zapewnia ciągły kontakt tylnich kół z podłożem

Rysunek 8: Koła robota

### 3.7 Obciążniki

Dociążenie konstrukcji okazało się być konieczne, ponieważ konstrukcja uzbrojona we wszystkie komponenty elektroniczne ważyła lekko ponad połowę maksymalnej (docelowej) masy. W roli obciążników zastosowano płyty ołowiane. Z uwagi na komfort użytkownika, ołów został owinięty czarną taśmą izolacyjną (brak kontaktu skóry z ołowiem).

(a) płyta ołowiana o grubości 2mm, obciążniki: mały 85g, duży 152g


(b) nakrętki umieszczone w sześciokątnych gniazdach ułatwiających przykręcanie
(c) obciążniki pełnią rolę dna korpusu, nisko położony środek ciężkości
(d) każdy z obciążników jest wykonany z dwóch warstw ołowiu o łącznej grubości 4mm

Rysunek 9: Obciążniki ołowiane

## 4 Elektronika

### 4.1 Płytka główna

Płytka wyposażona w główne komponenty została zaprojektowana początkowo w Autodesk Inventor (tak jak cały robot), a następnie po wyznaczeniu możliwego obrysu i wymiarów mechanicznych został wykonany projekt w programie KiCad 5. Ścieżki pomieściły się na dwóch warstwach miedzi, co zapewnia niskie koszty produkcji płytki PCB. Elementy zostały umiejscowione tak, aby znajdowały się po jednej stronie co ułatwiało montaż (z jednym wyjątkiem). Czarny kolor został wybrany wyłącznie dla walorów estetycznych.


(a) widok z przodu,
ekran OLED został wylutowany


(b) projekt w programie KiCad 5

Rysunek 10: Płytka główna

Mikrokontroler

Jako mikrokontroler został wybrany STM32F405 z uwagi na wcześniejsze doświadczenia z tą jednostką oraz możliwość jego zakupu (w sierpniu 2021 roku wybór w sklepach nie był obfity). Zostało wykorzystane sprzętowe wsparcie dla czterech enkoderów inkrementalnych.


Rysunek 11: Schemat wyprowadzeń mikrokontrolera, oscylator, zworka wyboru zasilania, przycisk reset, złącze programatora

Mostki H

Do sterownia silników użyto czterech dwukanałowych sterowników DRV8835. Został polecony przez znajomych, którzy zachwalali jego niewielkie rozmiary oraz stosunkowo dobre parametry (maksymalny prąd dwóch zmostkowanych kanałów 3A). Rzeczywiście, niewielka obudowa ułatwiła tworzenie projektu, ponieważ wymagał on dwukrotnie większej liczby takich układów (zazwyczaj konstrukcje tego typu mają dwa koła).


Rysunek 12: Schemat czterech układów z zmostkowanymi wyjściami, gniazda podłączeń silników

Pamięć nieulotna

Kość pamięci EEPROM ma na celu zapis stanu robota podczas walki, aby przy chwilowym braku zasilania lub wystąpieniu szpilki napięcia resetującą mikrokontroler (wywołaną nagłym uderzeniem) móc przywrócić maszynę stanów, dane o walce lub inne parametry do pamięci RAM.
Element ten został dodany do projektu jako ostatni w lekkim pośpiechu, więc został umieszczony na spodniej stronie płytki pomiędzy gniazdami podłączeń silników.


Rysunek 13: Schemat pamięci EEPROM

Zasilanie

W konstrukcji zostały wyszczególnione 3 rodzaje napięć:

- napięcie zasilania (bateryjne, max 11V) służące do zasilania mostków H i silników
- napięcie 5V (przejściowe) do zasilania modułu bluetooth
- napięcie 3.3V (logiczne) służące do zasilania mikrokontrolera, czujników i interfejsów


Rysunek 14: Schemat sekcji zasilania, od lewej: wejście baterii i ochrona przed odwrotną polaryzacją, włącznik główny, przetwornica 5V, stabilizator 3.3V, dzielnik do pomiaru napięcia baterii, dioda LED

Interfejs

W celu ułatwienia użytkowania, rozwoju i debugowania robota, zostały dodane:

- ekran OLED SSD1306 wraz z trzema przyciskami (interfejs graficzny)
- odbiornik podczerwieni wraz z żółtą diodą (wbudowany moduł startowy)
- moduł bluetooth HC-05 (możliwość wchodzenia w tryb AT z poziomu kodu)
- UART oraz dioda (debugowanie)


Rysunek 15: Schemat interfejsów od lewej: 3 przyciski, 2 diody, UART, moduł bluetooth, ekran, odbiornik IR

### 4.2 Czujniki linii

Do wykrycia białej linii na czarnym tle zostały wybrane popularne czujniki KTIR0711S w postaci klonów modułów QTR-1A (https://botland.com.pl/czujniki-odbiciowe/918-czujnik-odbiciowy-ktir0711s-modul-5904422351410.html) oryginalnie produkowanych przez firmę Pololu. Moduły okazały się być bardzo awaryjne i konieczna była wymiana scalaków na nowe (można było to przewidzieć po dwukrotnie niższej cenie za sztukę). W roli przewodów posłużyły trójżyłowe i giętkie kable odcięte od szeroko dostępnych 9-gramowych serwomechanizmów stosowanych w modelarstwie. Wtyk jest standardową listę pinów o rastrze 2,54 mm. Nóżki gniazda na płytce głównej zostały przed wlutowaniem uformowane tak, aby listwa żeńska nie ocierała o tarcze enkoderów.


(a) czujniki wraz kablem od serwomechanizów | (b) podłączenie czujników do płytki głównej

Rysunek 16: Czujniki linii

### 4.3 Enkodery

Kąt wychylenia koła można wyznaczyć poprzez zliczanie impulsów enkodera inkrementalnego. Do wybrango silnika przystosowane są enkodery (https://botland.com.pl/enkodery/4884-zestaw-enkoderow-magnetycznych-do-micro-silnikow-pololu-kompatybilne-z-hpcb-27-18v-2-szt-pololu-3081-5904422309763.html) także od firmy Pololu. Charakteryzują się 12 impulsami na obrót silnika, co razem z przekładnią 30:1 daje 360 impulsów na obrót koła (1◦
).
Niewielki raster wyprowadzeń 2mm uniemożliwia zastosowanie standardowych konektorów i listw 2.54mm, więc przylutowane zostały przewody taśmowe odzyskane ze starego komputera PC. Na linie zasilania silnika zostały użyte cztery żyły zmostkowane parami w celu minimalizacji oporu i wydzielanego ciepła.
Gniazda i konektory to standardowe listwy 2.54mm wybrane głównie z uwagi na niski profil (wyższe gniazda dawałby zbyt mało miejsca na baterię).
(a) enkoder (zielony) wraz z tarczą (czarną) zamontowany na silniku (srebrny)
(b) podłączenie wiązek silników do płytki głównej

Rysunek 17: Enkodery

### 4.4 Czujniki wykrycia przeciwnika

Z braku na rynku czujników wykrywania przeszkód i obiektów o zadowalających parametrach, cenie i rozmiarze zostały opracowane i stworzone własne sensory.
Początkowo planowane było zastosowanie pary dioda IR + fototranzystor bazując na robocie typu micromouse „Squick”[1], jednak wstępne testy wykazały zbyt niskie możliwości wykrywania obiektów oddalonych powyżej 20cm (pożądany zasiąg to 40cm).
Ostatecznie zostały zrealizowany pomysł jeszcze z roku 2019, w którym dioda nadawcza zasilana sygnałem prostokątnym o częstotliwości 48kHz wysyłała światło podczerwone, które po odbiciu od przeszkody wracał do sensora i był wykrywane przez popularny odbiornik TSOP4838. Konstrukcja ta osiągała zamierzone 40cm zasięgu oraz była łatwa i prost w budowie.
W celu implementacji do robota minisumo częstotliwość na której pracował czujnik musiała zostać zmienionana 56kHz, ponieważ 38kHz jest używane do nadawania wiadomości do modułów startowych przez sędziego. Nadawanie w tym paśmie mogłoby być powodem dyskwalifikacji robota z zawodów.
Wymiary zewnętrzne zostały zbliżone do rozmiaru czujnika JS40F. (https://www.jsumo.com/js40f-digital-infrared-ir-distance-sensor-min-40-cm-range) Wymusiło to niewielki rozmiar płytki PCB, która została zaprojektowana oraz ręcznie spanelizowana w programie KiCad 5.
Doświadczalne dobranie rezystora ograniczającego prąd diody nadawczej okazało się być wymagane, ponieważ zastosowany układ 555 w roli generatora przebiegu prostokątnego według dokumentacji (teoretycznie) nie powinien być zasilany napięciem 3.3V. Powodowało to nieprzewidywalną obciążalność prądową wyjścia i spadek napięcia.


(a) gotowy czujnik,
widoczny odbiornik i dioda nadawcza
(b) panelizacja płytki PCB

Rysunek 18: Czujnik wykrycia przeciwnika


Rysunek 19: Schemat płytki czujnika, od lewej: dioda nadawcza i generator przebiegu prostokątnego, odbiornik i wyjścia

## 5 Program

Program początkowo tworzony był w zintegrowanym środowisko STM32CubeIDE z wykorzystaniem bibliotek HAL oraz generatora kodu CubeMX. Po przejściu na śurowąŚTM-kę z programowaniem na rejestrach, projekt został przepisany na wykorzystanie systemu czasu rzeczywistego FreeRTOS w edytorze VSCode.

### 5.1 Budowa programu

Program został oparty o pojęciu "maszyny stanów", której przejścia pomiędzy stanami są zależne od informacji docierającej do robota. Główne wyodrębnione stany:

- Ready | – inicjalizacja peryferiów, oczekiwanie na sygnał
- Program | – parowanie z pilotem sędziego
- Run | – konstrukcja rozpoczęła algorytm walki sterowany odrębną maszyną stanów
- Stop 1 | – stan zabezpieczający przed odbezpieczeniem zasilania robota w warunkach nagłego
| zatrzymania silników np.: szok elektromagnetyczny, zakłócenia zasilania (dotyczy
| głównie większych konstrukcji)
- Stop 2 | – stan unieruchomienia robota, wymagane ponowne uruchomienie

Emulator modułu startowego

W celu uniknięcia potrzeby montowania modułu startowego w gotowego robota, konstrukcja została wyposażona w odpowiedni odbiornik IR oraz żółtą diodę led.
Paczki danych są zakodowane sygnałem RC5, który mikrokontroler odczytuje, co pozwala na rozszerzenie funkcji robota do bycia swoim własnym modułem startowym.

PROGRAM; START; Ready; reset; Program; STOP; Run; 1 second; Stop 1; Stop 2

Rysunek 20: Schemat UML maszyny stanów podczas kontroli konstrukcji odbiornikiem RC5

### 5.2 Algorytm walki

Algorytm walki w większości polega na znalezieniu przeciwnika (szczególnie w kategoriach minisumo enchanted, gdzie średnia dyhlo osiąga 1.54m). Po nawiązaniu pierwszego kontaktu, stery przejmuję kontroler PID, który dąży do utrzymania kursu robota na wprost przeciwnika.

timeout; enemy spotted; Follow; turning in last direction where enemy was spotted; enemy lost; Fight; move towards the enemy with PID controller; line spotted; Explore; move slowly straight ahead; Measure; estimate relative angle to center; Turn; rotate by the specific angle

Rysunek 21: Schemat UML maszyny stanów podczas walki

Estymacja pozycji przeciwnika

Konstrukcja zawiera 4 czujniki wykrywający obecność przeciwnika w zakresie ±90◦
. Znajomość tego które
czujniki zgłaszają wykrycie obiektu i założenia, że na ringu znajduje się tylko jeden przeciwnik oraz dostępna przestrzeń ogranicza się do płaszczyzny ringu, pozwala na określenie przybliżonego kąta obecności przeciwnika względem kierunku frontu robota.
Odbywa się to poprzez nadanie wartości katów poszczególnym czujnikom (w tym przypadku są to od lewej: −90◦

, −30◦

, 30◦

, 90◦
), a następnie wykonanie średniej arytmetycznej z wszystkich wartości, których czujniki stwierdziły wykrycie obiektu.

Estymacja pozycji względem krawędzi ringu

Przy założeniu, że krawędź ringu jest linią prostą (dla dużych promieni ringu generuje to mały błąd), nie występują poślizgi kół oraz że sytuacja nie jest ękstremalna"(kąt jest bliski ±90◦
), możliwe jest przybliżenie kąta pod jakim robot najeżdża na styczną do krawędzi ringu i o jaki kąt powinien skręcić, aby powrócić na środek planszy (kierunek prostopadły do stycznej krawędzi w punkcie położenia robota).
Robot posiada cztery czujniki wykrycia linii: dwa przy końcach ostrza (zewnętrzen), dwa przy centrum ostrza (wewnętrzne). Po wykryci linii na którymś z zewnętrznych czujników odbiciowych, robot zwalnia tempo poruszania i zliczając impulsy enkoderów mierzy odległość którą przebywa do momentu wykrycia linii czujnikiem wewnętrznym.
Znając odległość pomiędzy daną parą czujników wewnętrznych i zewnętrznych Dcz = const i przejechany dystans d kąt najechania na krawędź θn i kąt wymaganego obrotu θo wynoszą odpowiednio:

θnajazdu = tan⁻¹

d

Dcz
θobrotu = π − θnajazdu

## 6 Zdjęcia


(a) widok z przodu | (b) widok z boku
(c) widok od tyłu | (d) widok z dołu
(e) widok z góry | (f) widok z góry przy odtwartej obudowie
(g) widok pod skosem z przodu | (h) widok pod skosem od tyłu

Rysunek 22: Konstrukcja złożonego robota

## 7 Podsumowanie

Projekt jako realizacja przemyśleń na temat czterokołowego robota klasy minisumo został wykonany w większości po myśli konstruktora. To co na początku wydawało się być problemem np. solidność kadłuba wydrukowanego z PLA, okazało się być całkowicie przesadzonymi obawami.
Od początku konstrukcja miała być wykonana profesjonalnymi metodami, całkowicie unikając tz. „rzeźbienia”. Początkowy model 3D przeszedł bardzo długą drogę do moment aż wydał się możliwy do zrobienia. Nakreślił on ograniczenia mechaniczne nałożone na całą elektronikę (bateria, czujniki). Gdyby pominąć wielokrotne próby kompensowania precyzji wydruków z użytej drukarki, wszystkie elementy pasowałby do siebie za pierwszym razem.
Założenie w którym płytka główna jest osobnym elementem do którego za pomocą przewodów wpinane są czujniki i efektory okazało się sprawiać więcej problemów niż pożytku. Powoduje to zmniejszanie się już i tak niewielkiej przestrzeni o przewody i gniazda, które cechują się dużą awaryjnością. Utrudnia to również szybki demontaż konstrukcji w celu nagłej naprawy.
Warto wspomnieć, że mimo braku świadomego wzorowania się na robocie „Enova”[5], zmiany wprowadzane do projektu powoli oddalały go od początkowego zamysłu właśnie w tą stronę. Wielokrotnie można było usłyszeć od starszych zawodników opinie, że jest to konstrukcja wzorowana na „Enovie”, co z uwagi na jej osiągnięcia można uznać za komplement. Faktem jest natomiast to, że wspomniany robot udowadnia, że można stworzyć wybitną konstrukcję minisumo wyposażoną w 4 koła.
Jednak mimo to odpowiedź na pytanie: „Co jest lepsze w minisumo, dwa czy cztery koła?” jest proste: dwa koła. Mimo wcześniejszej niepewności, która dała początek temu projektowi, praktyka pokazuje, że dwa koła dają zdecydowanie większą manewrowość, zmniejsza koszt o dwie jednostki napędowe oraz zwiększa ilość dostępnego miejsca na baterię i czujniki.
W konstrukcji czterokołowej pojawiają się takie problemy jak: brak lub mały docisk ostrza do płaszczyzny ringu, nierówny docisk kół do podłoża, pojawia się tarcie boczne działające na koła przy skrętach.

## 8 Odnośnik do repozytorium GIT

Projekt od początku właściwych prac jest dokumentowany na repozytorium GIT: https://github.com/Eryk-Mozdzen/minisumo-sneak100. (https://github.com/Eryk-Mozdzen/minisumo-sneak100)

## Bibliografia

[1] Piotr Gorzelnik i Patryk Szydlik. Robot mobilny typu MicroMouse ”Squick”. 2021.
[2] Eryk Możdżeń. Robot mobilny klasy minisumo ”Scalak”. 2021. url: https://github.com/Eryk-Mozdzen/minisumo-scalak/blob/main/docs/raport/Dokumentacja_MS_Scalak.pdf. (https://github.com/Eryk-Mozdzen/minisumo-scalak/blob/main/docs/raport/Dokumentacja_MS_Scalak.pdf)
[3] Krzysztof Pochwała. Robot mobilny klasy minisumo ”Flash”. 2015. url: https : / / forbot . pl / forum / topic/8309-minisumo-flash/. (https://forbot.pl/forum/topic/8309-minisumo-flash/)
[4] Devex Robotics. Mini Sumo, from design to competing in Robot SM 2019. url: https://www.youtube.com/watch?v=_aM-ktyTo84. (https://www.youtube.com/watch?v=_aM-ktyTo84)
[5] Magnat Cyber Forge Team. Enova. 2014. url: https://forbot.pl/forum/topic/7020-enova/.

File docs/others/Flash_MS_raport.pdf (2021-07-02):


Robot mobilny klasy minisumo

## ”Flash”

Krzysztof Pochwała

Koło Naukowe Robotyków KoNaR

www.konar.pwr.edu.pl

29 stycznia 2015

SPIS TREŚCI | SPIS TREŚCI

## Spis treści

1 Wstęp | 2
2 Konstrukcja mechaniczna | 3
3 Elektronika | 6
4 Zakończenie | 14

1

1 WSTĘP

## 1 Wstęp

Celem niniejszego raportu jest przybliżenie konstrukcji robota minisumo Flash. Głównym celem jego budowy było poznanie nowych rozwiązań sensorycznych i algorytmicznych. Ponadto robot powstawał w okresie warsztatów rekrutacyjnych do koła naukowego robotyków KoNaR, których ukończenie jest warunkiem koniecznym do bycia przyjętym w szeregi tegoż. Ogromne podziękowania należą się drużynieMagnat Cyber Forge Team za to, że udostępnili opis swojego robota Enova[1] oraz Karolowi Sydorowi za udostępnienie raportu z budowy robota Shine[2].

2

2 KONSTRUKCJA MECHANICZNA

## 2 Konstrukcja mechaniczna

### 2.1 Założenia projektowe

Konstrukcja mechaniczna robota została zaprojektowana w programie Autodesk Inventor 2014 (początkowo również w Solid Edge ST4). Pozwoliło to na zoptymalizowanie rozmiarów robota i maksymalne upakowanie elementów wewnątrz obudowy. Głównym założeniem podczas projektowania obudowy było to, aby była jak najniższa i tak bardzo jak to tylko możliwe utrudniała wykrycie robota przez czujniki przeciwnika. Wysokością, którą autor uznał za nieprzekraczalną był 1 cal (25,4mm), co udało się uzyskać, gdyż robot w najwyższym punkcie mierzy 22mm. Ponadto wszystkie ścianki są pochylone pod kątem co najmniej 45 stopni, a cała obudowa jest pokryta matową farbą proszkową.


Rysunek 1: Rendering robota

3

2.2 Obudowa | 2 KONSTRUKCJA MECHANICZNA

### 2.2 Obudowa

Obudowa robota składa się z trzech głównych elementów - korpusu, pokrywy i dokręcanego do gniazda w korpusie pługu. Elementy te zostały wykonane ze stali narzędziowej na frezarce CNC. Materiał pozwolił uzyskać odpowiednia dla robota minisumo wytrzymałość i masę, natomiast dzięki zastosowanej technologii obróbki możliwe stało się uzyskanie nietypowych kształtów.


(a) Korpus | (b) Pokrywa i ostrze

Rysunek 2: Obudowa robota

W korpusie zostały wyfrezowane gniazda na silniki i elektronikę, wykonane zostały równiez otwory na dalmierze i śruby m3 skręcające całego robota. Pokrywa a została wyposażona w otwory na moduł startowy, głośniczek, i interfejs. Gniazdo w korpusie pozwala na zastosowanie wymienialnych ostrz pługa (niestety na chwilę obecną zastosowane jest ręcznie robione ostrze z mosiądzu, które wcale nie jest ostre).

4

2.3 Napęd | 2 KONSTRUKCJA MECHANICZNA


Rysunek 3: Wnętrze robota z widoczną częścią wyposażenia

### 2.3 Napęd

Robota napędzają dwa mikrosilniki DC z przekładniami firmy Pololu. Przełożenie 30:1. Aby uzyskać lepszą odpowiedź silników wyposażone zostały w enkodery magnetyczne tego samego producenta oraz ich sterowniki zasilane są napięciem 11,1V z akumulatora Li-Pol 3S. Wykorzystany mikrokontroler jest wyposażony w sprzętowe wsparcie dla enkoderów, co zostało wykorzystne. Koła, które zostały użyte to przerobione felgi solarbotics z oponą odlaną z silnikonu formierskiego o twardości 16ShA. Rozdzielczość odczytu przemieszczenia robota z zastosowanymi enkoderami to 0,19mm. Silniki blokowane są w ich gnieździe za pomocą czterech śrub m3 bez łba (tzw. robaczków).

5

3 ELEKTRONIKA


(a) Enkoder na silniku | (b) Felga z oponą

Rysunek 4: Pojedynczy zespół napędowy

## 3 Elektronika

### 3.1 Czujniki

Robot wyposażony jest w szereg czujników:

1. Czujniki przeciwnika
2. Czujniki linii
3. Enkodery
4. Akcelerometr i Żyroskop

### 3.1.1 Czujniki przeciwnika

Najważniejszym są czujniki przeciwnika. Zostały one wykonane samodzielnie z diod IR OPE5594A i fototranzystorów TEFT4300. Nadajniki zostały dobrane ze względu na szerokość wiązki, moc światła i możliwość pracy w impulsach o dużym prądzie. Pod uwagę brane były również TSAL6400 i LD271, jednak wybrane OPE w zestawieniu wypadły najlepiej. Rozwiązanie to jest wzorowane na robotach ”Insumountable”[3] i ”Stealth2”[4] Petera Wallera, oraz ”Shine”[2] Karola Sydora.
Zasada działania jest prosta. Diody oświetlają przestrzeń dookoła robota, a fototranzystory mierzą ile światła, które robot wyemitował powraca do niego. Dzięki zastosowaniu mikrokontrolera wyposażonego w rdzeń Cortex-M4, a co z tym idzie w jednostkę FPU i dodatkowe instrukcje DSP możliwe jest zastosowanie filtrów cyfrowych, zmniejszając tym samym ilość elementów na PCB i dodając walorów edukacyjnych. Całe przetwarzanie sygnałów

6

3.1 Czujniki | 3 ELEKTRONIKA

dokonywane jest w programie, jedynym elementem biernym w torze odbiorczym jest rezystor przy fototranzystorze, dzięki któremy sygnał prądowy z fototranzystora zamieniany jest na napięciowy, który następnie trafia do przetwornika ADC mikrokontrolera (12 bit, 2,4MSPS). Rezystor dobrany jest tak, by odbiornik działał cały czas w liniowej części swojej charakterystyki (nie nasycał się). Jedyny element aktywny to wspomniany fototranzystor. Nadajniki załączane są na bardzo krótki okres czasu (50µs), aby zmaksymalizować emitowana przez nie moc. Do sterowania diodami nadawczymi zostały zastosowane w dość niestandardowej aplikacji drivery tranzystorów MOSFET TC4427. Są one w stanie dostarczać diodom 1,5A w impulsie.


Rysunek 5: Schemat dalmierzy

Jak widać, w robocie zostało zastosowane w sumie 7 dalmierzy. Dzięki temu, że pola widzenia sąsiednich się w pewnym stopniu pokrywają, możliwe jest dość dokładne okreslenie pozycji przeciwnika względem środka robota. Jest to uchyb podawany na regulator PID, którego zadaniem jest utrzymanie przecwnika na wprost pługa.

7

3.1 Czujniki | 3 ELEKTRONIKA

### 3.1.2 Czujniki linii

Czujniki linii to popularne transoptory odbiciowe KTIR0711S podłączone bezpośrednio do przetwornika ADC mikrokontrolera. Z mikrokontrolera mozna również sterować diodami transoptorów - czy mają być zapalone, czy zgaszone. Pozwala to na pomiar różnicowy i eliminację zakłóceń powstałych np. z nierównomiernego oświetlenia ringu, jego nagrzania lub innego wolnozmiennego promieniowania podczerwonego.


Rysunek 6: Schemat czujników linii

Cztery złącza z lewej strony schematu to połączenie z płytką główną robota. Pierwszy blok to czujniki umieszczone z tyłu, a następny to czujniki umieszczone z przodu. Złącza pomiędzy blokami to złacza pomiędzy płytkami - pozostawienie linii łączących oba pozwoliło na uzycie wbudowanego w oprogramowanie Eagle polecenia DRC (Design Rule Check) sprawdzającego restrykcje projektu PCB.

8

3.1 Czujniki | 3 ELEKTRONIKA


Rysunek 7: Płytki czujników linii

Robot jest wyposażony w sumie w 8 czujników przeciwnika, po 2 na każdy róg robota. Dzięki temu, robot może oszacować kąt, pod jakim najechał na linię i odbić się od niej w kierunku środka ringu. Znana jest odległość pomiędzy czujnikami, znana jest również odległość, jaką robot przejechał od zobaczenia linii czujnikiem zewnętrznym do zobaczenia jej wewnętrznym -na tej podstawie można skonstruować trójkąt prostokątny i przy pomocy trygonometrii obliczyć interesujący nas kąt. Jest to rozwiązanie zaczerpnięte z robota Enova.

### 3.1.3 Enkodery

Podłączenie enkoderów do robota jest trywialne. Na płytce przylutowanej do silnika znajdują się następujące wyjścia:

sygnał | opis
GND | ujemny biegun zasilania enkodera
B | wyjście B enkodera
A | wyjście A enkodera
VCC | dodatni biegun zasilania enkodera
M2 | zacisk silnika
M1 | zacisk silnika

Tabela 1: Przyłącza silników

Jak widać na poniższym renderingu, PCB enkoderów są przylutowane

9

3.1 Czujniki | 3 ELEKTRONIKA

bezpośrednio do płytki głównej - w gnieździe silników absolutnie nie było miejsca na poprowadzenie przewodów.


Rysunek 8: Połączenie enkoderów z płytką główną

Wyjścia A i B enkoderów podłączone są do zewnętrznych wejść liczników, a te z kolei ustawione są na obsługę enkoderów inkrementalnych. Dzięki temu ich obsługa w ogóle nie obciąża jednostki centralnej. Wystarczy z odpowiednich rejestrów odczytać aktualną wartość licznika - jeśli silnik kręci się w jedną stronę licznik zwiększa się, jeśli w przeciwną zmniejsza.

### 3.1.4 Akcelerometr i żyroskop

W robocie jest miejsce na IMU produkcji ST Microelectronics - LSM330DH. Niestety przez nieuwagę w projekcie PCB została uzyta błędna obudowa niż ta, która została zakupiona, co uniemożliwiło jak na razie jego wykorzystanie. Jego zamontowanie motywowane było tym, by robot znał swoją orientację w przestrzeni nie tylko na podstawie odometrii opartej o enkodery. Ponadto mozliwe byłoby wykrywanie uniesienia i wykonywanie uników. W planach było zastosowanie filtra Kalmana w celu fuzji sygnałów z akcelerometru (zaszumiony, szybkozmienny) i żyroskopu (gładki, ale obarczony stale

10

3.2 Płytka główna | 3 ELEKTRONIKA

narastającym błędęm wynikającym z dryftu). Byłoby to sprzężenie zwrotne dla regulatora odpowiedzialnego za orientację robota względem przeciwnika.

### 3.2 Płytka główna

Jednostką obliczeniową robota jest mikrokontroler STM32F407VGT6. Rdzeń Cortex-M4 został wybrany ze względu na dużą moc obliczeniową (210 DMIPS przy 168MHz). Ponadto wyposażony jest w jednostkę zmiennoprzecinkową i podstawowe instrukcje DSP. Te cechy umożliwiają zastosowanie zaawansowanych algorytmów, a duża pamięć wewnętrzna (1MB) pozwala na ciągłe rozwijanie kodu. Zastosowany został również ze względu na to, że dokładnie ten sam model jest na płytkach STM32F4 Discovery, co pozwoliło na bezpośrednie przenoszenie kodu pomiędzy płytką ewaluacyjną a robotem w celu sprawdzenia poprawności programu. W planach jest ciągłe rozwijanie algorytmów.


Rysunek 9: Otoczenie mikrokontrolera

11

3.2 Płytka główna | 3 ELEKTRONIKA

Ponadto, na płytce głównej znajdują się pola lutownicze dla diod i fototranzystorów czujników przeciwnika, szereg diod kontrolnych - obecność zasilania silników, obecność zasilania logiki robota, dioda połączona z tranzystorem sterującym diodami czujników linii i wolna dioda podłączona do jednego z pinów GPIO mikrokontrolera ułatwiająca debugowanie kodu na wczesnym etapie jego powstawania. Zamianą napięcia z akumulatora na 3,3V dla logiki zajmuje się przetwornica impulsowa D24V6F3 firmy Pololu. Na płytce nie została wylana masa ze względu na to, że ścieżki zasilania prowadzone są zgodnie z topologią gwiazdy i łączą się w jednym punkcie. Ponadto masa i zasilanie części analogowej robota (przetwornika ADC mikrokontrolera, fototranzystory dalmierzy) odseparowane są od swoich cyfrowych odpowiedników dławikami 10µH.
Na płytce znajduje się też szereg złącz. Są to konektory do płytek czujników linii, interfejsu i złącze SWD służące do programowani i debugowania mikrokontrolera.
Na centralnej PCB znajdują się także sterowniki silników. Są to układy Toshiby TB6612FNG w standardowej aplikacji ze zmostkowanymi kanałami zwiększającymi wydajność prądową układu (przy okazji zmniejszając rezystancję wewnętrzną tychże).


Rysunek 10: Projekt płytki głównej

12

3.3 Interfejs | 3 ELEKTRONIKA

### 3.3 Interfejs

W celu komunikacji ze światem zewnętrznym zaprojektowana została płytka, składana ”na kanapkę” z płytką główną. Na niej mieści się multiplekser 74HC164 podłaczony do szyny SPI mikrokontrolera, którego wyjścia są z kolei podłączone do diod LED. Dzięki temu używając tylko dwóch linii (SCK i MOSI) możemy sterować ośmioma diodami, czyli wyświetlać 256 różnych kombinacji (na dwóch liniach byłyby tylko 4). Dzięki wykorzystaniu sprzętowego interfejsu, zmiana stanów diod może odbywac się bez obciążania jednostki centralnej programową implementacją protokołu SPI.


Rysunek 11: Schemat interfejsu

Robot wyposażony został również w niewielki głośniczek, który jest podłączony do jednego z wolnych wyjść driverów TC4427. Sterowany jest on jednym z timerów mikrokontrolera.
Na tej samej płytce umieszczone zostało także złącze dla standardowego modułu startowego, obowiązkowego w kategorii minisumo. Jest też złącze akumulatora wraz z zabezpieczeniem przed odwrotną polaryzacją i wyłącznik (szybkie odłaczenie akumulatora nie wchodzi w grę, ze względu na zamknięcie go w obudowie skręcanej śrubami).

13

LITERATURA

## 4 Zakończenie

Jest to jak na razie najbardziej skomplikowany robot jakiego projektowałem. Absolutnie nie jest w myśl zasady KISS (Keep It Simple, Stupid), co zaowocowało podczas uruchamiania. Na zawodach robot wystartował ślepy, gdyż czujniki przeciwnika nie były jeszcze dokończone, co oczywiście skutkowałem pozostaniem w grupie. Okazało się jednak, że część robotów miała problem z zauważeniem go. Za jeden z większzych błędów uważam zastosowanie mikrokontrolera w obudowie LQFP100 - katorga podczas lutowania i wysoka cena. Jednak ten błąd okazał się ułatwieniem gdy na 2-3 dni przed zawodami mikrokontroler uległ uszkodzeniu wskutek zwarcia jednego pinu z plusem akumulatora (TB6612 ma piny PWM i VMOT obok siebie, zostały zmostkowane i mikrokontroler nie przetrwał). Jako, że miałem pod ręką Discovery, szybko naprawiłem usterkę. W kolejnej rewizji PCB (a na pewno powstanie, ze względu na IMU i kilku mniej ważnych błedów naprawionych kynarem) zastosuję mikrokontroler w mniejszej obudowie.

## Literatura

[1] Magnat Cyber Forge Team (publikował Krzema). | [Minisumo] Eno-
va Minisumo’. | http://www.forbot.pl/forum/topics7/minisumo-enova-
minisumo-vt9961.htm?sid=b7a63e015be55a65dd4b315b21374526, 2014.
[2] Karol Sydor. | Raport z budowa robota mobilnego klasy minisumo
”Shine”. | http://konar.pwr.edu.pl/index.php/pobieralnia/category/9-
minisumo?download=53:shine, 2009.
[3] Peter | Waller | (PeterW). | Insumountable. | http://er-
online.co.uk/minisumo/forum/viewtopic.php?f=6&t=261&sid=2efeba90c3c97b500221e470b0cd0d38, 2007.
[4] Peter | Waller | (PeterW). | Stealth2. | http://er-
online.co.uk/minisumo/forum/viewtopic.php?f=6&t=433&sid=793ff5f2f3e601062f2e739f666ce47a, 2008.

14

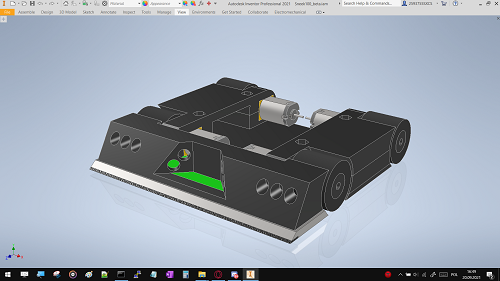
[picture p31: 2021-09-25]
docs/raport/images_mechanics/sneak100_concept_beta.png

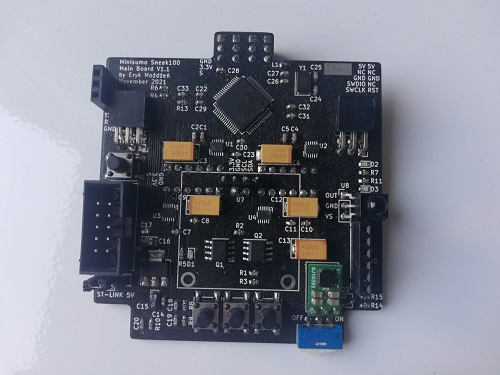
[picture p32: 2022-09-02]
docs/raport/images_electronics/board_front.jpg

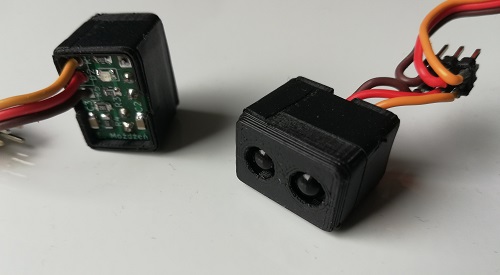
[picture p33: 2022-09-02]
docs/raport/images_mechanics/prox_1.jpg

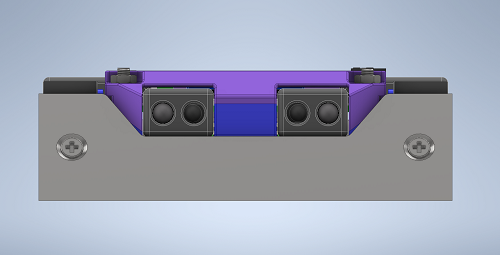
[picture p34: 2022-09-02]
docs/raport/images_mechanics/project3d_front.png

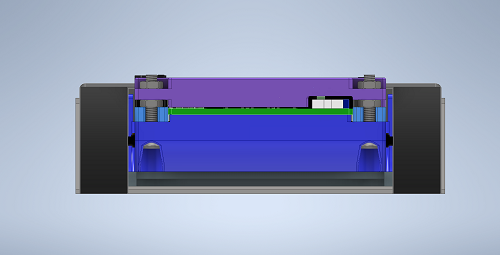
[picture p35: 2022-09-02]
docs/raport/images_mechanics/project3d_back.png

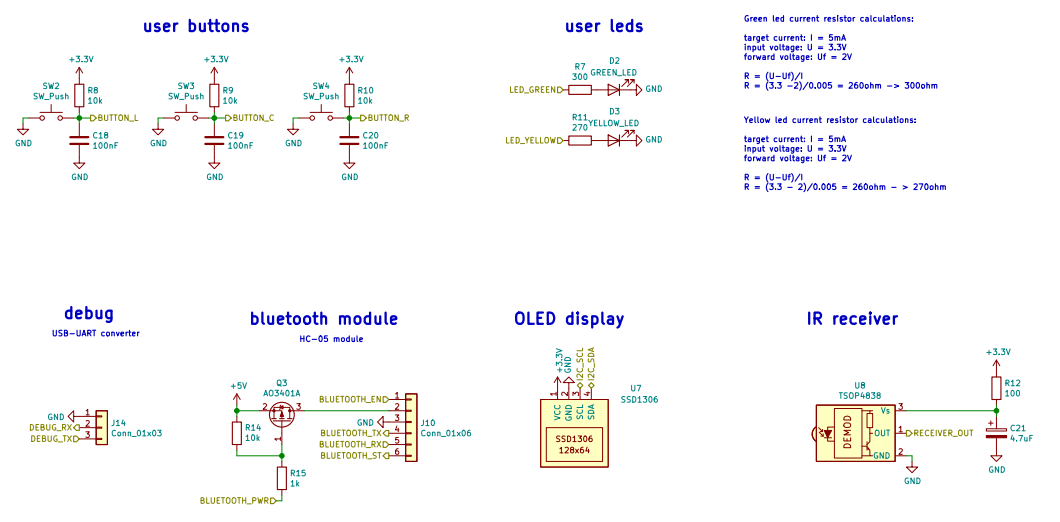
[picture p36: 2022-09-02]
docs/raport/images_electronics/scheme_interface.PNG

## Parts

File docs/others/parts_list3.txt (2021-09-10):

Jacktronic:
zamówienine
2	Tranz.AO4407				3,80	7,60

10	Kond.SMD4,7uF(100szt) 0603 16V X5R	12.00

izolacyjne rurki termokurczliwe		opakowanie

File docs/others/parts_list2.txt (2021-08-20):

Sneak100:
4	DRV8835DSSR				5,50	22
1	Kwarc 8.000 MHz 5x3,2mm 2PAD SMD	3	3
2	Tranz.AO4407				3,80	7,60
1	MODUŁ BLUETOOTH HC05			36	36
1	US LM1117IMP-3.3 SOT223			1,50	1,50

2	Rez.SMD 1K(100szt) 0603 1%		3	3
16	Rez.SMD 10K(100szt) 0603 1%		3	3		+10 z czujnika
1	Rez.SMD 18K(100szt) 0603 1%		3	3
1	Rez.SMD 360R(100szt) 0603 1%		3	3
1	Rez.SMD 300R(100szt) 0603 1%		3	3
11	Rez.SMD 270R(100szt) 0603 1%		3	3		+10 z czujnika
11	Rez.SMD 100R(100szt) 0603 1%		3	3		+10 z czujnika

18	Kond.SMD100nF(100szt) 0603 25V X7R	15,01	
2	Kond.SMD2,2uF(100szt) 0603 10V X5R	6
2	Kond.SMD22pF(100szt) 0603 50V COG 5%	5,01
1	Kond.SMD1uF(100szt) 0603 16V X7R 10%	5,01
1	Kond.SMD4,7uF(100szt) 0805 10V X7R	17
13	Kond.tantal.SMD 4,7uF/16V A		0,50	6,50		+10 z czujnika
5	Kond.tantal.SMD 47uF/20V D 10%		1,40	7

1	dławik SMD 4,7uH 0805/0603
1	Dioda LED SMD 0603 RED			0,20	0,20
1	Dioda LED SMD 0603 GREEN		0,25	0,25
1	Dioda LED SMD 0603 YELLOW 80mcd		0,20	0,20

	listwa goldpin raster 2,54mm żeńska kątowa
	listwa goldpin raster 2,54mm żeńska kątowa podwójna
10	Tulejka dys.z tworz.H= 4mm(100szt)	20

Proxima:
6	US NE555 ?				2,50	15
10	Kond.SMD47nF(100szt) 0805 50V X7R	10	10
10	Kond.SMD1,2nF(100szt) 0805.		5,01	5,01
10	Rez.SMD 47R(100szt) 0805		3	3
10	Rez.SMD 1,5K(100szt) 0805 1%		3	3
10	Rez.SMD 10K 0805 0,1%			3	3		mniejszy z robota
10	Rez.SMD 270R(100szt) 0805 1%		3	3		mniejszy z robota
10	Rez.SMD 100R(100szt) 0805 1%		3	3		mniejszy z robota
10	Kond.tantal.SMD 4,7uF/16V A		0,50	5		z robota

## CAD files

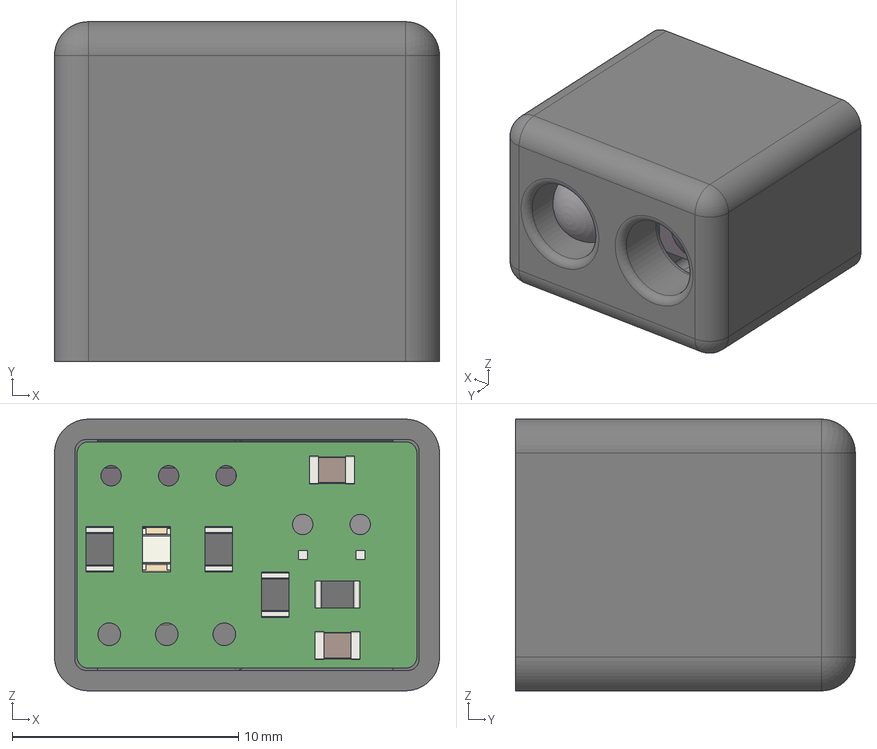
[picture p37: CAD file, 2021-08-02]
mechanics/ElectricElements/proxima_sensor_model.stp
17.0 x 15.0 x 12.0 mm
proxima_case
proxima_kicadSOLID_1
proxima_kicadSOLID_2
proxima_kicadSOLID_3
proxima_kicadSOLID_4 x 5
proxima_kicadSOLID_5
proxima_kicadSOLID_6
proxima_kicadSOLID_7 x 2
proxima_kicadCOMPOUND

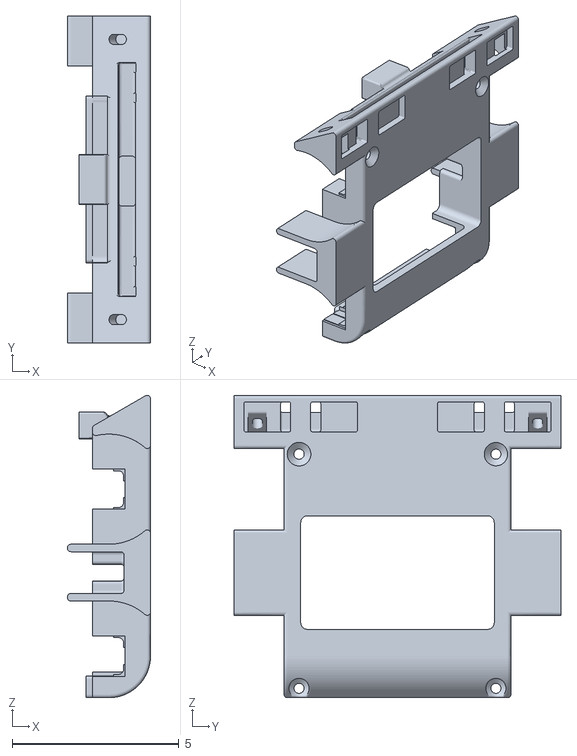
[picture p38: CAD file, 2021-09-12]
mechanics/stl_files/version_2/HullBottom.stl
2.49 x 9.80 x 9.06

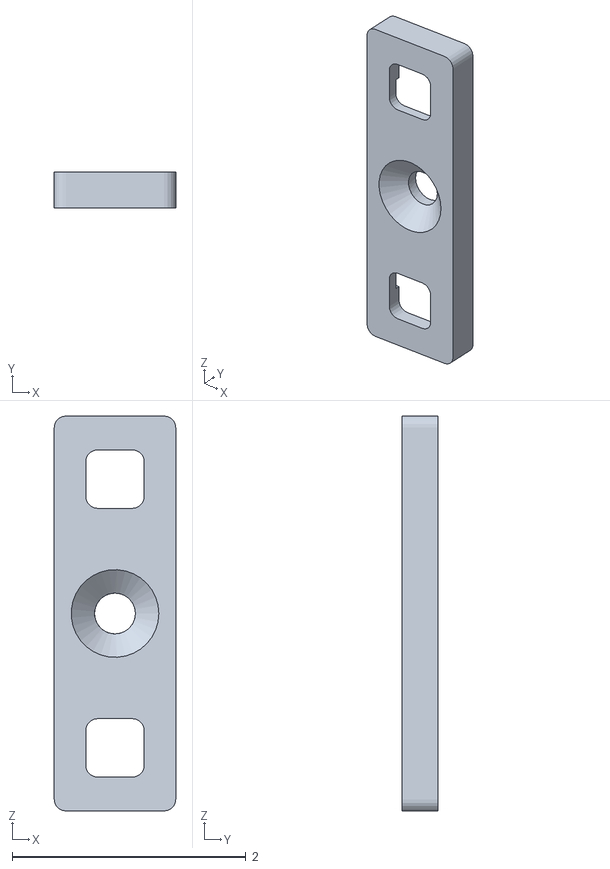
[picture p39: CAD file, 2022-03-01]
mechanics/stl_files/version_3_26_02_2022/LineSensorPlate.stl
1.04 x 0.31 x 3.38

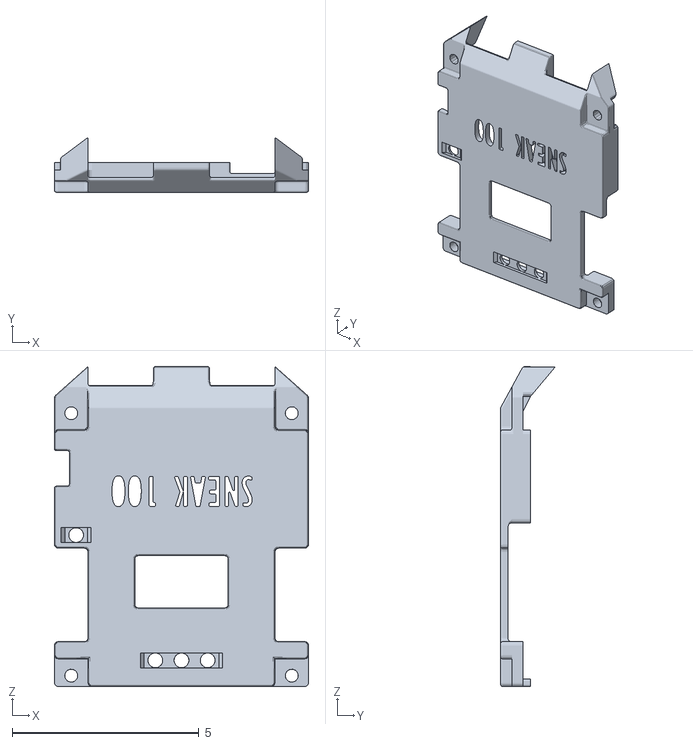
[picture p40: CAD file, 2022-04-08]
mechanics/stl_files/version_rybnik_2022/HullTop.stl
6.80 x 1.46 x 8.56

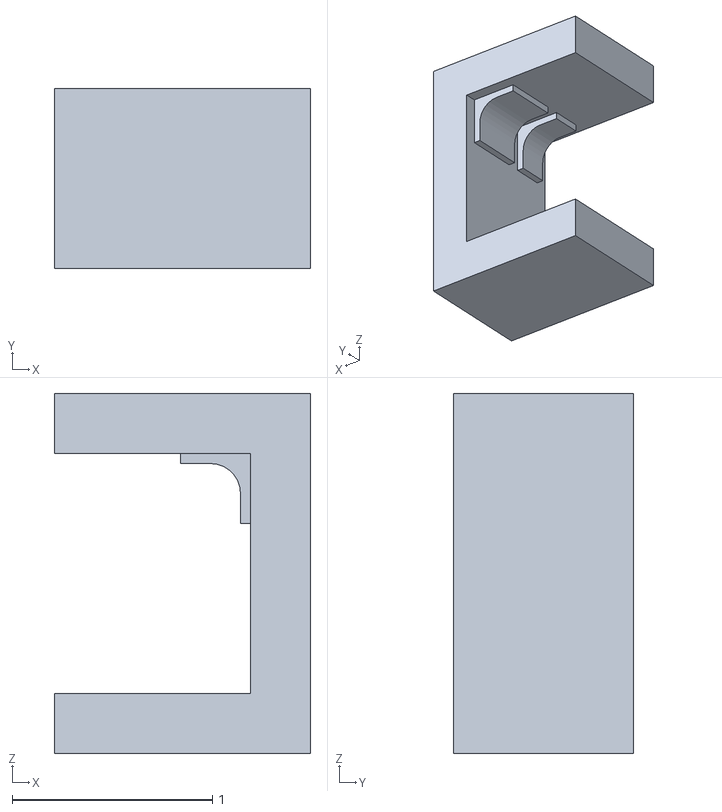
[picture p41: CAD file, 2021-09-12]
mechanics/stl_files/version_2/MotorMountTest.stl
1.28 x 0.9 x 1.80

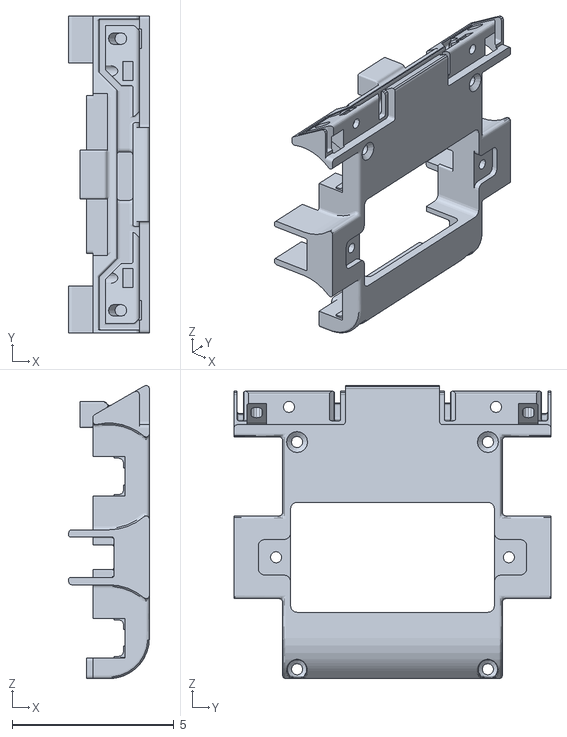
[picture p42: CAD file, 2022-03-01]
mechanics/stl_files/version_3_26_02_2022/HullBottom.stl
2.50 x 9.80 x 9.06

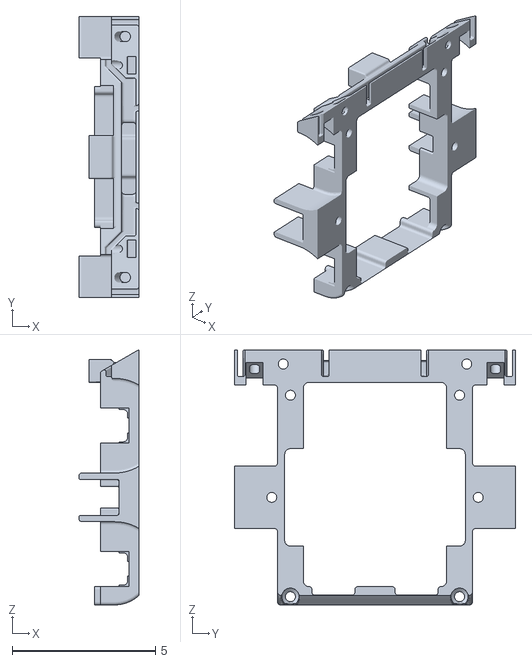
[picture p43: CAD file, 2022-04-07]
mechanics/stl_files/version_rybnik_2022/HullBottom.stl
2.10 x 9.80 x 8.89

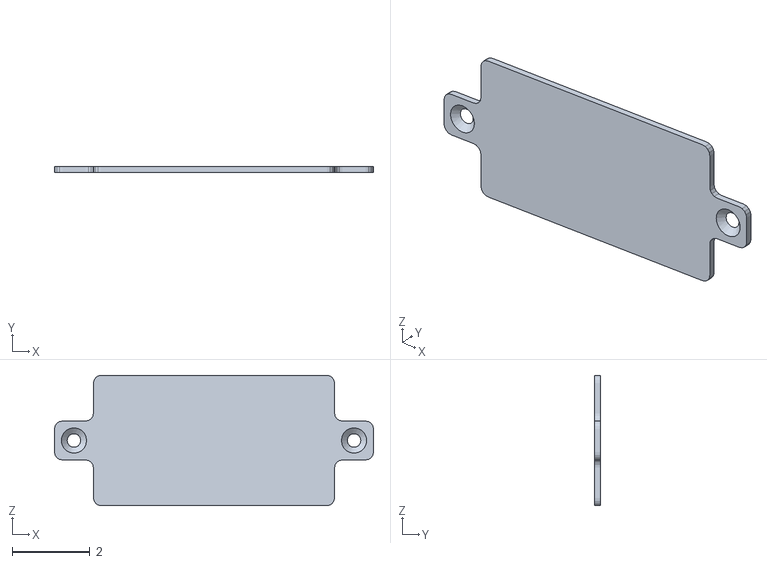
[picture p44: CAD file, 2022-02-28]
mechanics/stl_files/version_3_26_02_2022/BatteryPlate.stl
8.20 x 0.15 x 3.35

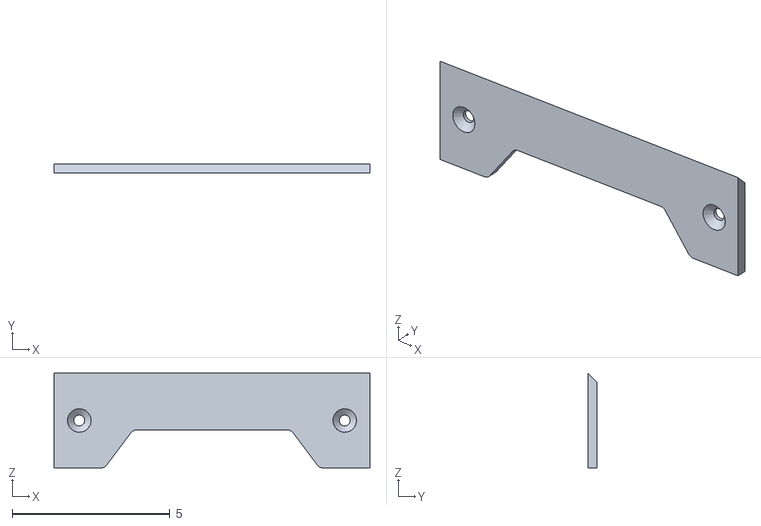
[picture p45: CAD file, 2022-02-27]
mechanics/stl_files/version_3_26_02_2022/HM_Knife_cut.stl
10.0 x 0.3 x 3.00

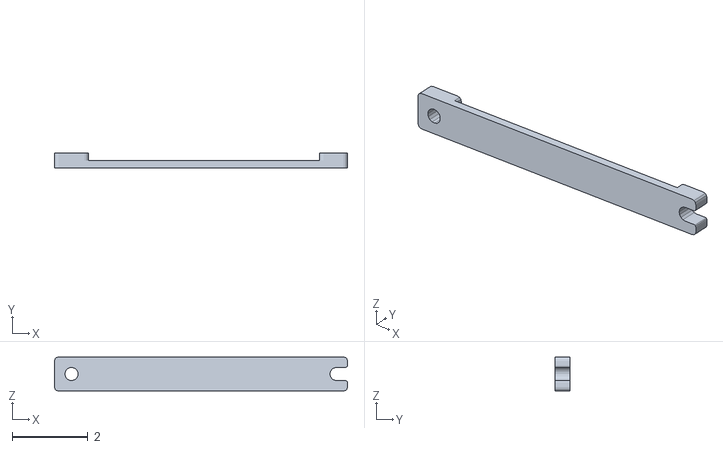
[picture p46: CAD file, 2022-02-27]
mechanics/stl_files/version_3_26_02_2022/HullMid.stl
7.76 x 0.4 x 0.9

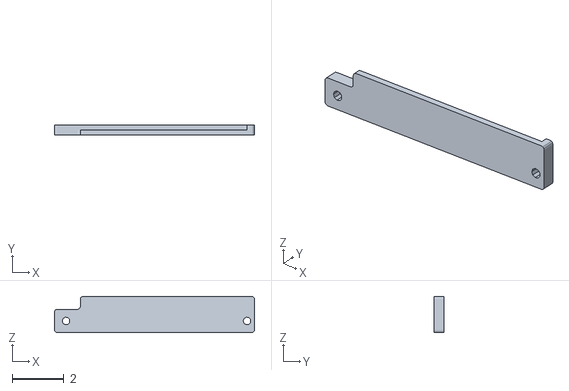
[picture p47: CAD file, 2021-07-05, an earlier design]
mechanics/stl_files/version_1/HullMid_MIR.stl
7.76 x 0.4 x 1.40

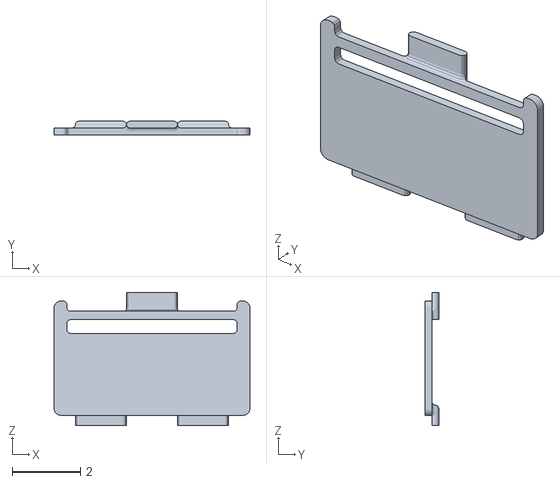
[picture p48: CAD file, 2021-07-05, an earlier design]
mechanics/stl_files/version_1/BatteryPlate.stl
5.76 x 0.4 x 3.91

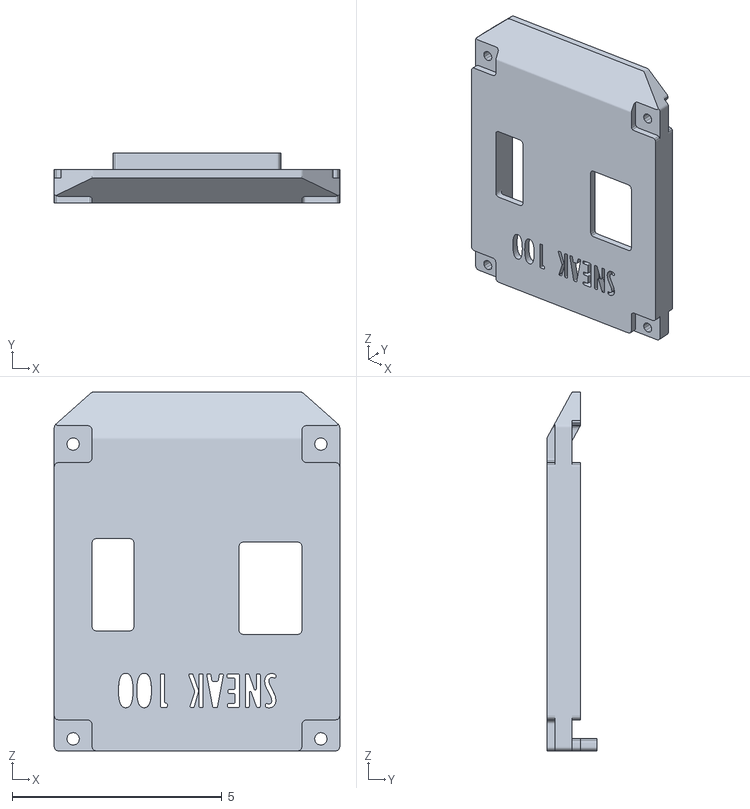
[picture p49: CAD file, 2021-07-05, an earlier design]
mechanics/stl_files/version_1/HullTop.stl
6.80 x 1.20 x 8.55

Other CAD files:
mechanics/stl_files/version_3_26_02_2022/HullTop.stl
mechanics/stl_files/version_1/HullMid.stl
mechanics/stl_files/version_1/HullBottom.stl
mechanics/ElectricElements/20NK_3-50CM.ipt
mechanics/ElectricElements/Battery[45x24x21].ipt
mechanics/ElectricElements/Battery[54x30_5x17_5].ipt
mechanics/ElectricElements/Battery[72x25x19].ipt
mechanics/ElectricElements/Battery[72x36x19].ipt
mechanics/ElectricElements/BistateSwitch_7x7mm_THT.ipt
mechanics/ElectricElements/CNY70.ipt
mechanics/ElectricElements/Dip_switch_4.ipt
mechanics/ElectricElements/FemaleHeaderPin_1x2.iam
mechanics/ElectricElements/FemaleHeaderPin_1x3.iam
mechanics/ElectricElements/FemaleHeaderPin_1x4.iam
mechanics/ElectricElements/FemaleHeaderPin_1x5.iam
mechanics/ElectricElements/FemaleHeaderPin_1x6.iam
mechanics/ElectricElements/FemaleHeaderPin_1x6_90.iam
mechanics/ElectricElements/FemaleHeaderPin_2x3_90.iam
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

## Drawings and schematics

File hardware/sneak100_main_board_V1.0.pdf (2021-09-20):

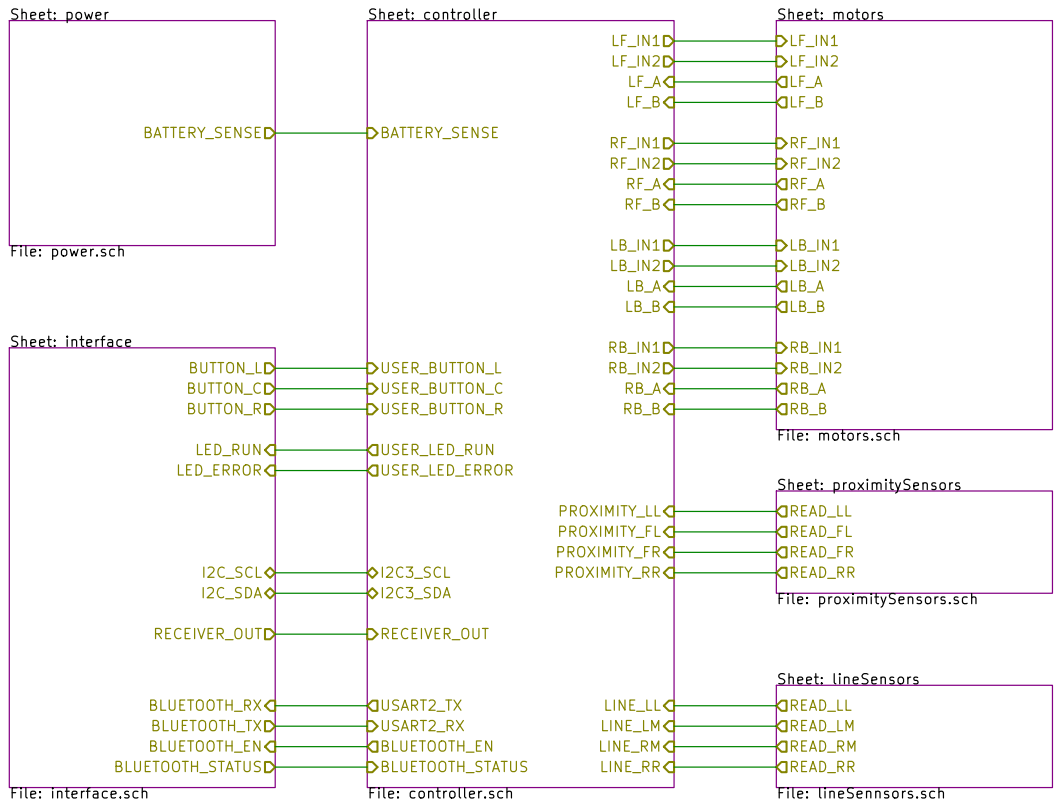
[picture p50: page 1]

Sheet: lineSensors File: lineSennsors.sch READ_LL READ_LM

File: sneak100_main_board.sch Sheet: /
Id: 1/7 Title: Sneak100 Main Board V1.0

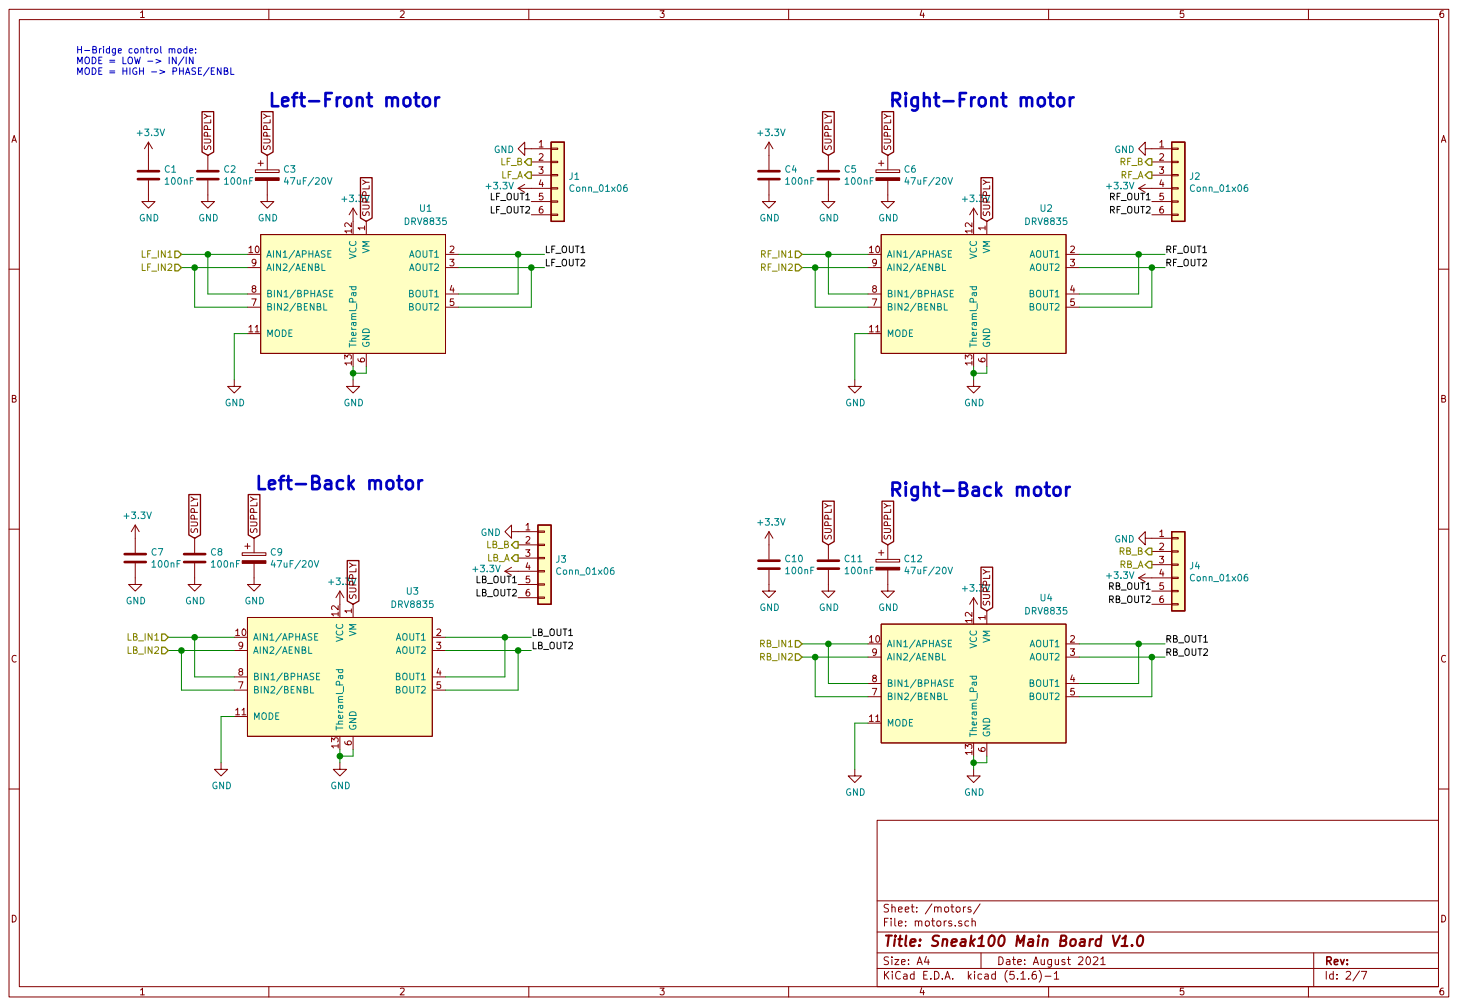
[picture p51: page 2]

H-Bridge control mode: MODE = LOW -> IN/IN MODE = HIGH -> PHASE/ENBL

6 BIN2/BENBL 7 BIN1/BPHASE 8 AIN2/AENBL 9 U1 DRV8835 GND

6 BIN2/BENBL 7 BIN1/BPHASE 8 AIN2/AENBL 9 U2 DRV8835 GND GND

1 AIN1/APHASE 10 MODE 11 VCC 12 Theraml_Pad 13 AOUT1 2 AOUT2 3 BOUT1 4 BOUT2 5 GND

Right-Back motor Left-Back motor

6 BIN2/BENBL 7 BIN1/BPHASE 8 AIN2/AENBL 9 U4 DRV8835 +3.3V GND 1

6 BIN2/BENBL 7 BIN1/BPHASE 8 AIN2/AENBL 9 U3 DRV8835 GND GND

File: motors.sch Sheet: /motors/
Id: 2/7 Title: Sneak100 Main Board V1.0

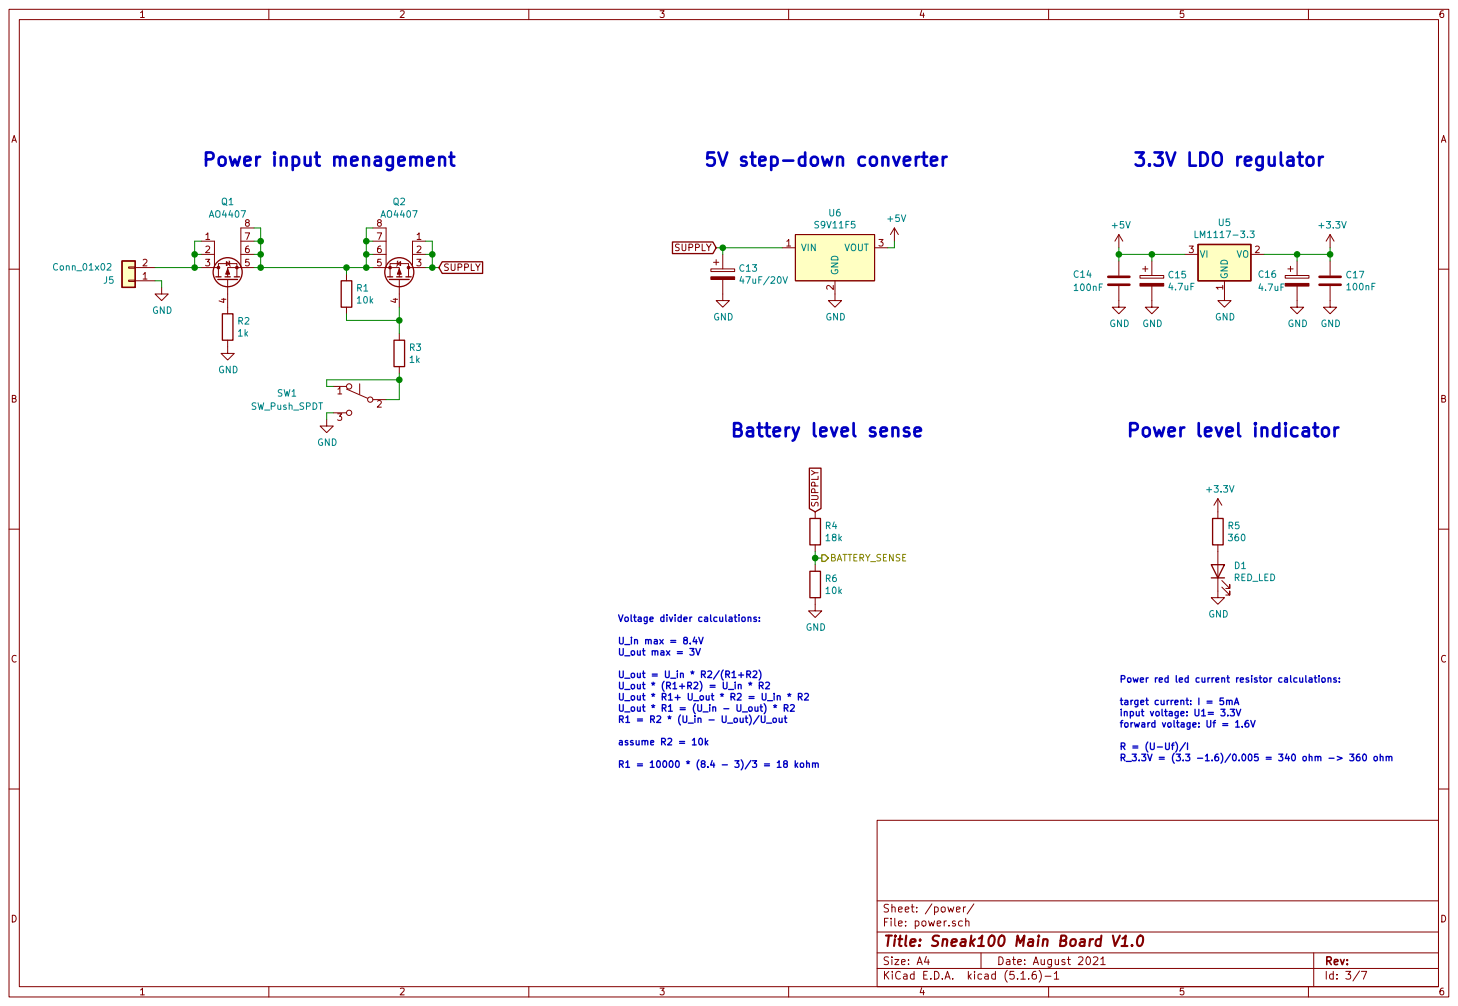
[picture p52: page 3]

Voltage divider calculations: U_in max = 8.4V U_out max = 3V U_out = U_in * R2/(R1+R2)

Power red led current resistor calculations:

Sheet: /power/
File: power.sch
Id: 3/7 Title: Sneak100 Main Board V1.0

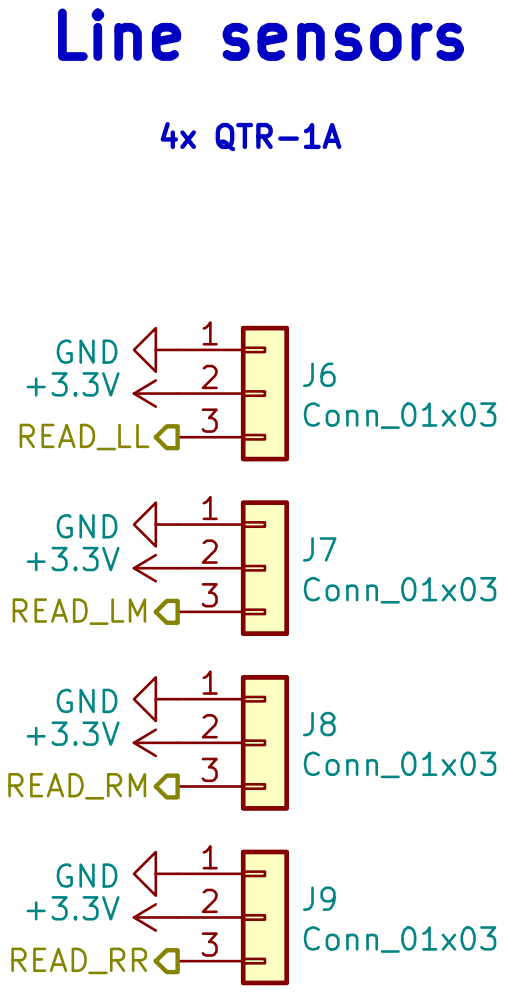
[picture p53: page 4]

File: lineSennsors.sch Sheet: /lineSensors/
Id: 4/7 Title: Sneak100 Main Board V1.0

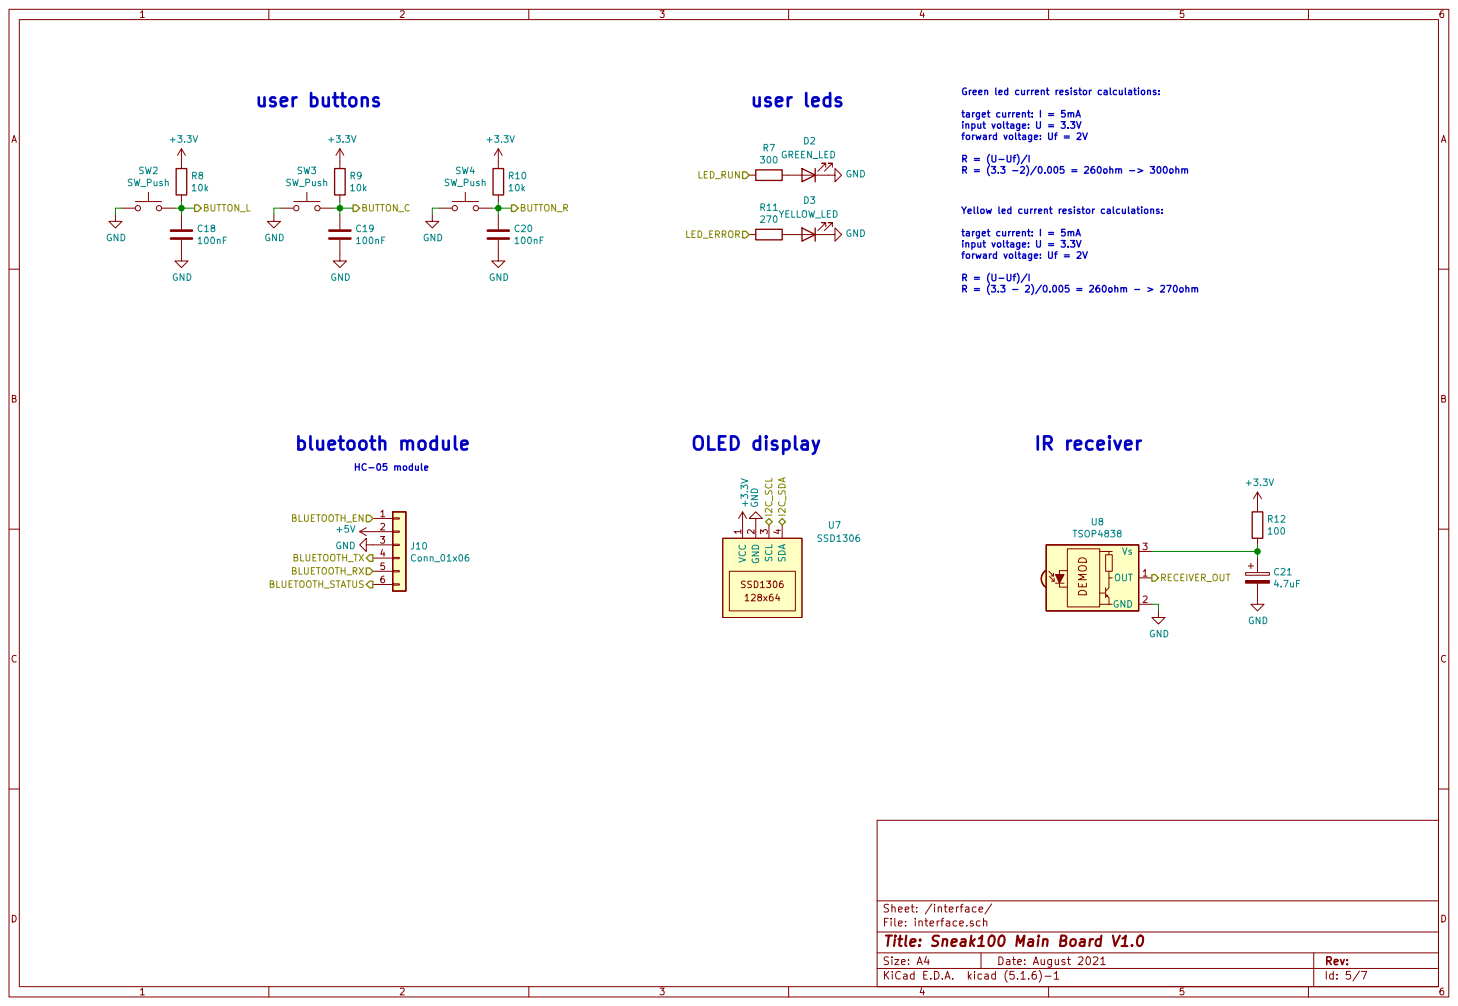
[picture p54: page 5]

File: interface.sch Sheet: /interface/
Id: 5/7 Title: Sneak100 Main Board V1.0

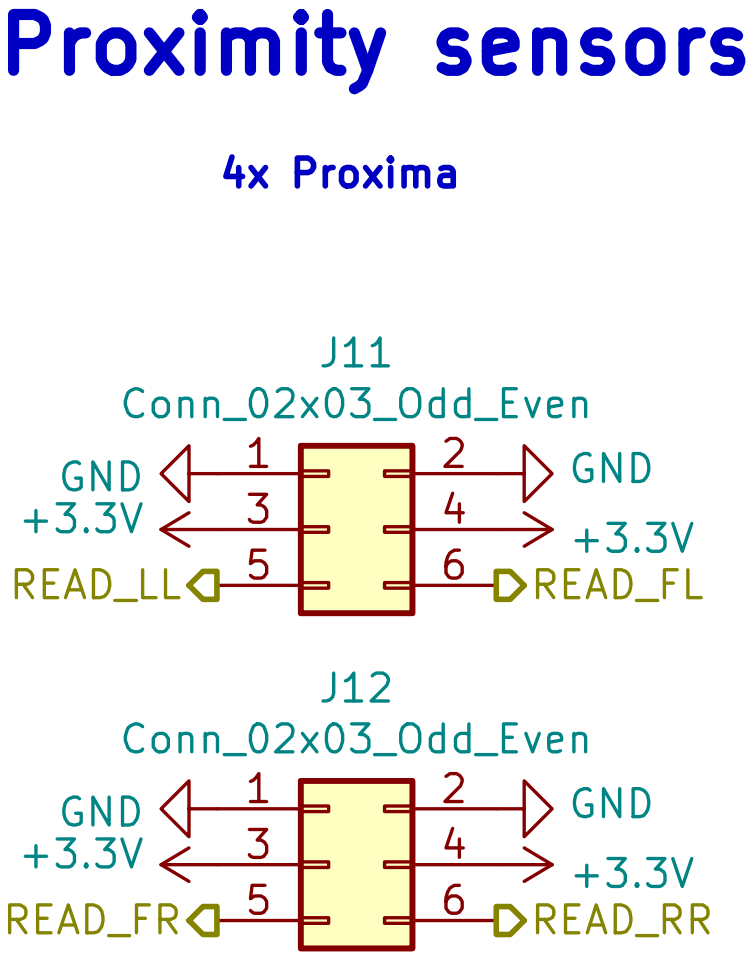
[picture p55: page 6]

Sheet: /proximitySensors/
File: proximitySensors.sch
Id: 6/7 Title: Sneak100 Main Board V1.0

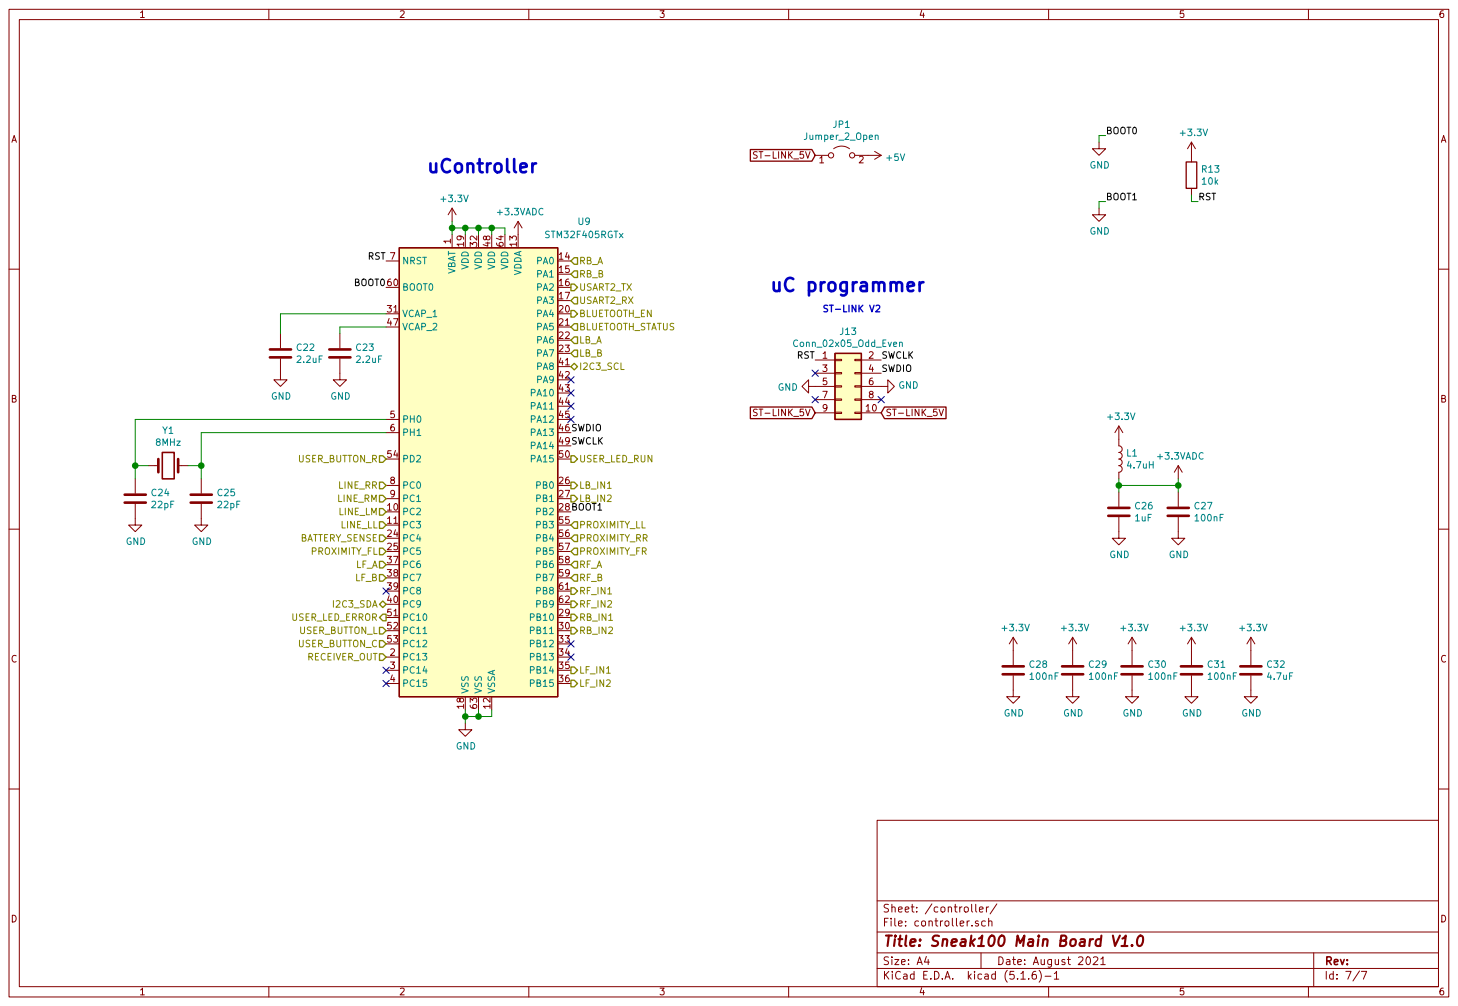
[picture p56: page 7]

1 VCAP_1 31 VCAP_2 47 VDD 19 VDD 32 VDD 48 VDD 64 VDDA 13 VSS 18 VSS 63 VSSA 12 U9 STM32F405RGTx 1

Id: 7/7 Title: Sneak100 Main Board V1.0

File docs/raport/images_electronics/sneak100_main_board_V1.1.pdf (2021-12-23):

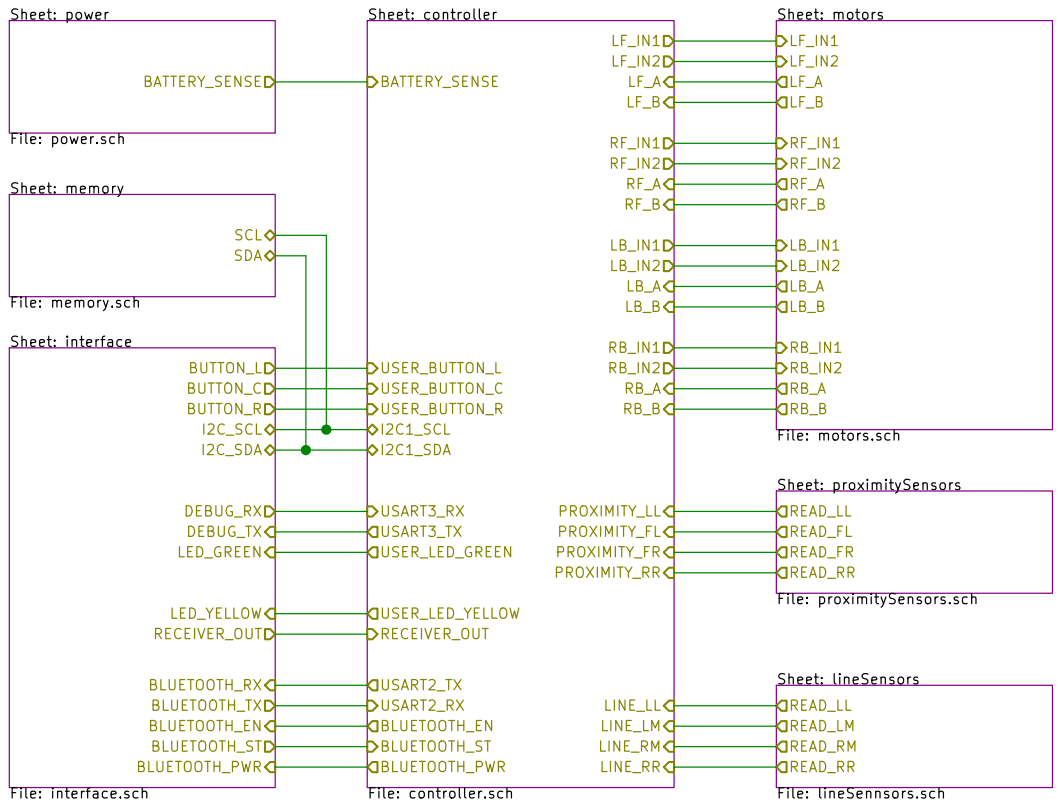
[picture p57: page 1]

File: sneak100_main_board.sch Sheet: / Sheet: lineSensors File: lineSennsors.sch READ_LL READ_LM

Id: 1/8 Title: Sneak100 Main Board V1.1

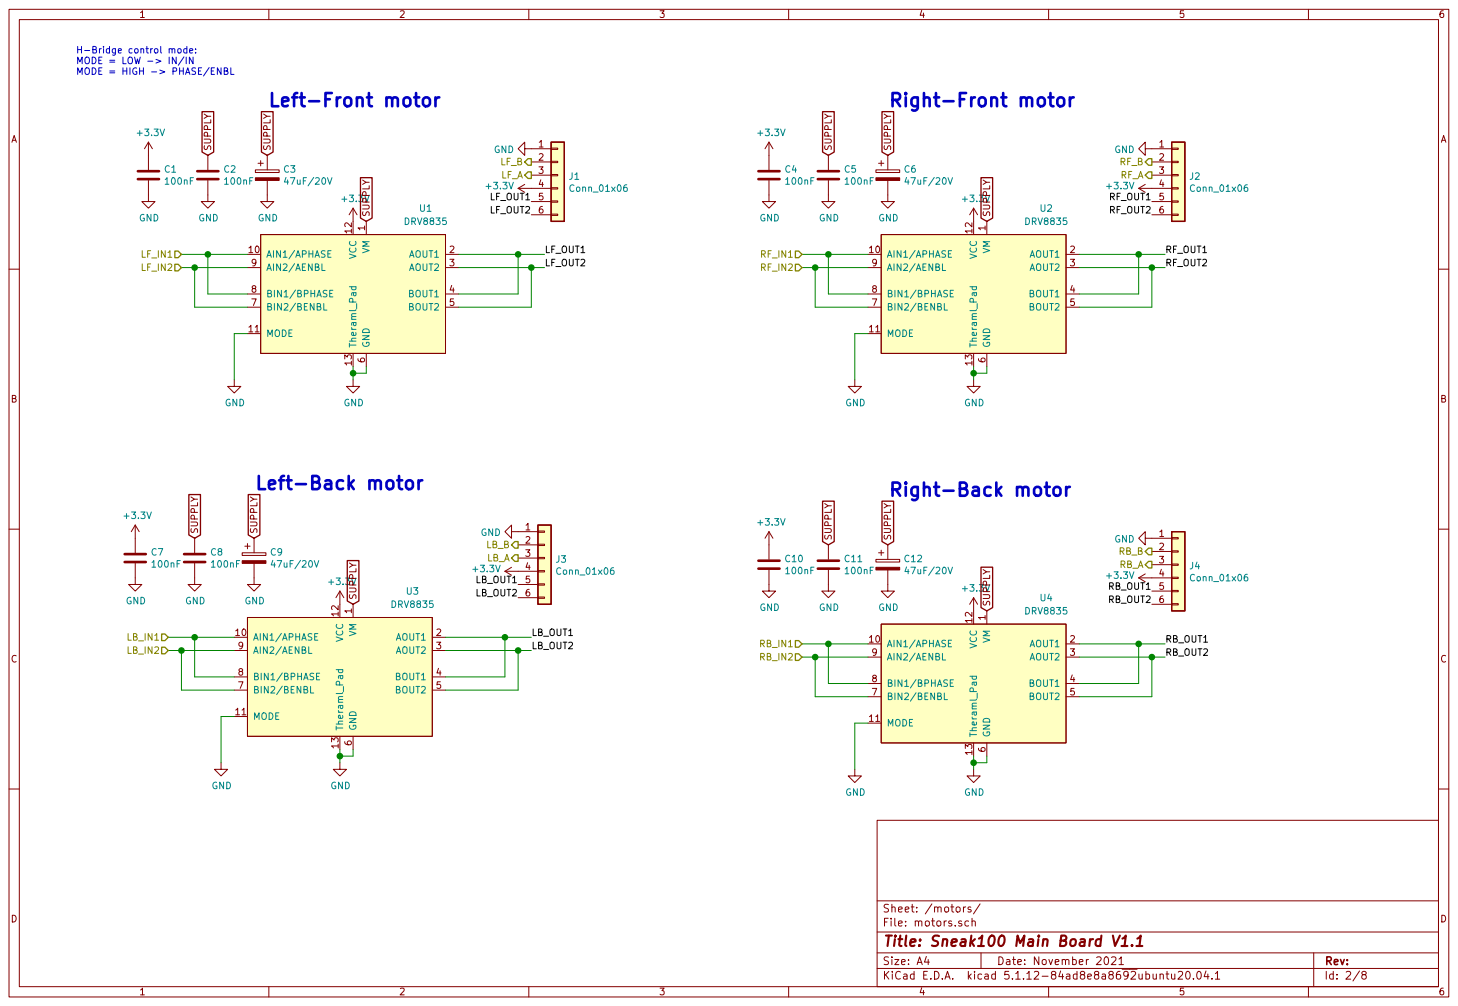
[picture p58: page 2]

H-Bridge control mode: MODE = LOW -> IN/IN MODE = HIGH -> PHASE/ENBL

6 BIN2/BENBL 7 BIN1/BPHASE 8 AIN2/AENBL 9 U1 DRV8835 GND

6 BIN2/BENBL 7 BIN1/BPHASE 8 AIN2/AENBL 9 U2 DRV8835 GND GND

1 AIN1/APHASE 10 MODE 11 VCC 12 Theraml_Pad 13 AOUT1 2 AOUT2 3 BOUT1 4 BOUT2 5 GND

Right-Back motor Left-Back motor

6 BIN2/BENBL 7 BIN1/BPHASE 8 AIN2/AENBL 9 U4 DRV8835 +3.3V GND 1

6 BIN2/BENBL 7 BIN1/BPHASE 8 AIN2/AENBL 9 U3 DRV8835 GND GND

File: motors.sch Sheet: /motors/
Id: 2/8 Title: Sneak100 Main Board V1.1


File: lineSennsors.sch Sheet: /lineSensors/
Id: 3/8 Title: Sneak100 Main Board V1.1


Sheet: /proximitySensors/
File: proximitySensors.sch
Id: 4/8 Title: Sneak100 Main Board V1.1

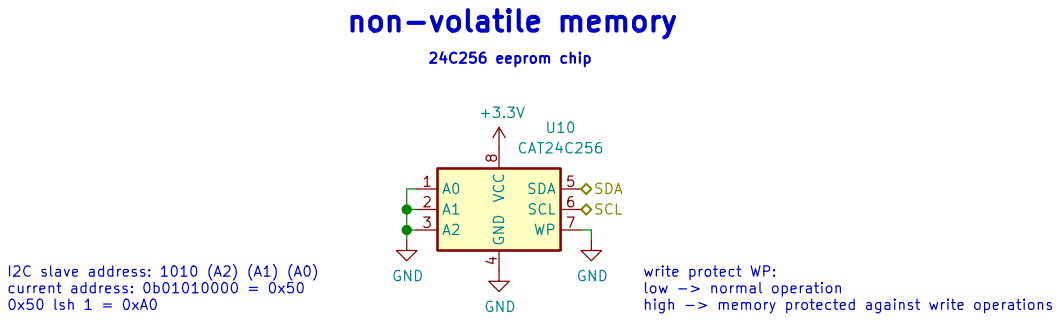
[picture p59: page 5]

4 SDA 5 SCL 6 WP 7 VCC

I2C slave address: 1010 (A2) (A1) (A0) current address: 0b01010000 = 0x50

low -> normal operation
high -> memory protected against write operations

File: memory.sch
Id: 5/8 Title: Sneak100 Main Board V1.1

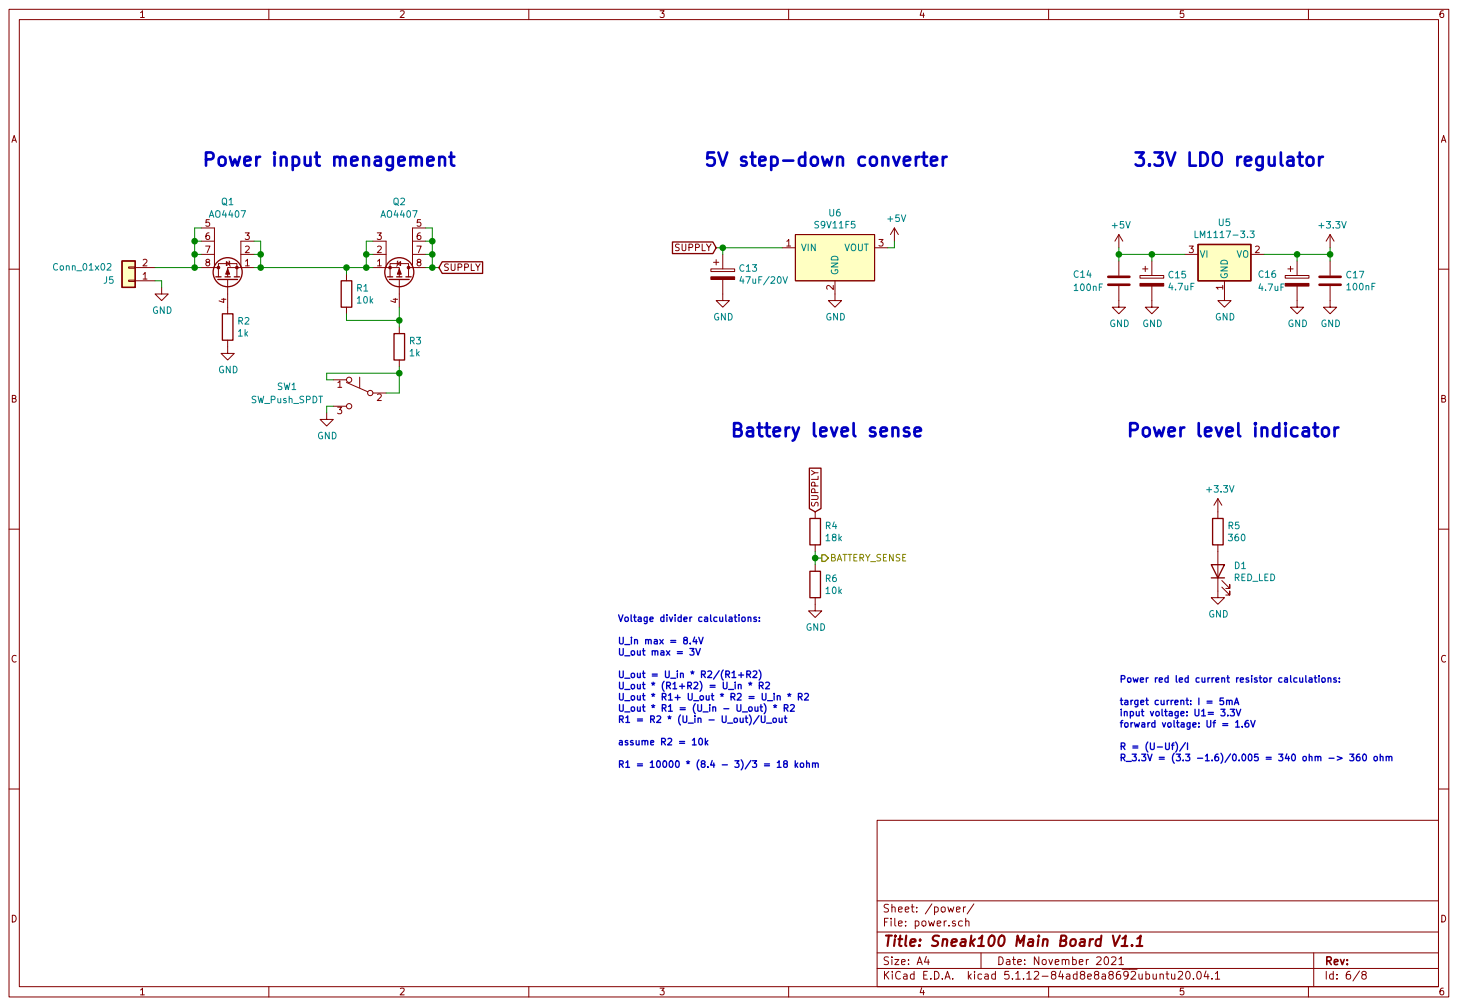
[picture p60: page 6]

SUPPLY Power input menagement

Voltage divider calculations: U_in max = 8.4V U_out max = 3V U_out = U_in * R2/(R1+R2)

Power red led current resistor calculations:

Sheet: /power/
File: power.sch
Id: 6/8 Title: Sneak100 Main Board V1.1

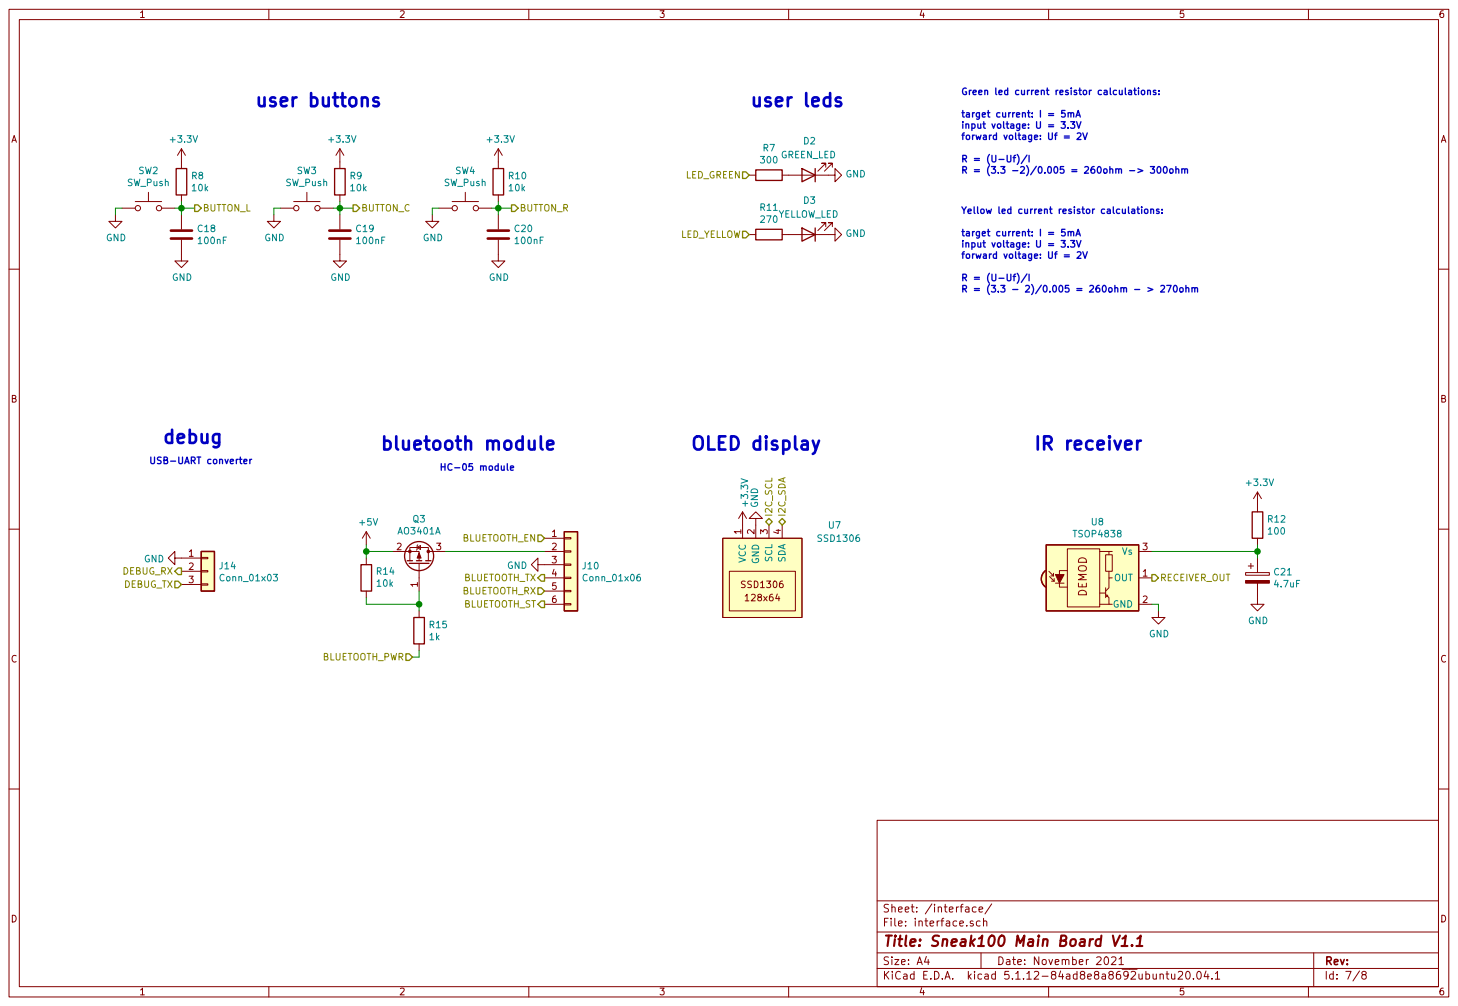
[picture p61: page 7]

Green led current resistor calculations:

Yellow led current resistor calculations:

HC-05 module USB-UART converter debug

File: interface.sch Sheet: /interface/
Id: 7/8 Title: Sneak100 Main Board V1.1


1 VCAP_1 31 VCAP_2 47 VDD 19 VDD 32 VDD 48 VDD 64 VDDA 13 VSS 18 VSS 63 VSSA 12 U9 STM32F405RGTx R13
BOOT0 SWCLK uController

ST-LINK V2 uC programmer

Id: 8/8 Title: Sneak100 Main Board V1.1

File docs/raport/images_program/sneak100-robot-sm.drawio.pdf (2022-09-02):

PROGRAM; START; Ready; reset; Program; STOP; Run; 1 second; Stop 1; Stop 2

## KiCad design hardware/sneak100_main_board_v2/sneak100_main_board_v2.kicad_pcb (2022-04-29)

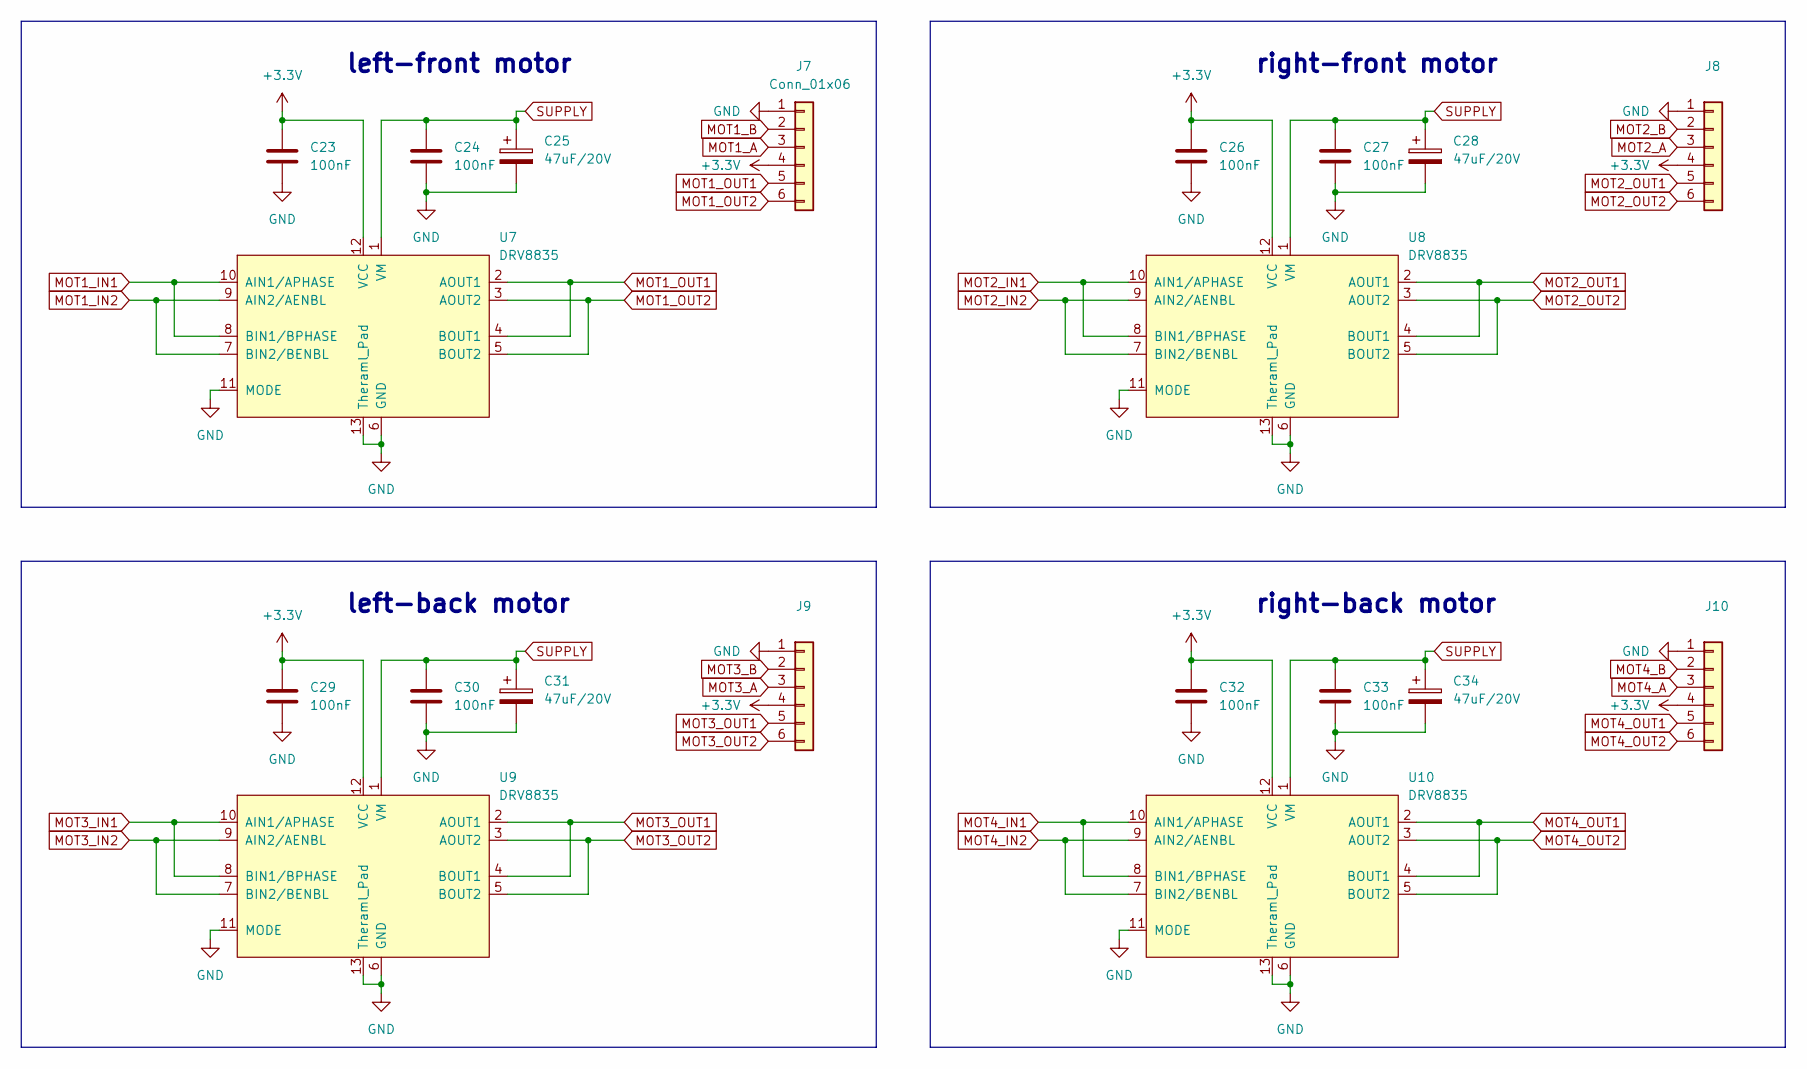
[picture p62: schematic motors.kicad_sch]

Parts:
C23, C24, C26, C27, C29, C30, C32, C33: 100nF
C25, C28, C31, C34: 47uF/20V
J7: Conn_01x06
J8, J9, J10: (no value)
U7, U8, U9, U10: DRV8835

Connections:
GND: C23.2, C24.2, C25.2, C26.2, C27.2, C28.2, C29.2, C30.2, C31.2, C32.2, C33.2, C34.2, J7.1, J8.1, J9.1, J10.1, U7.6 (GND), U7.11 (MODE), U7.13 (Theraml_Pad), U8.6 (GND), U8.11 (MODE), U8.13 (Theraml_Pad), U9.6 (GND), U9.11 (MODE), U9.13 (Theraml_Pad), U10.6 (GND), U10.11 (MODE), U10.13 (Theraml_Pad); also elsewhere on the board
MOT1_A: J7.3; also elsewhere on the board
MOT1_B: J7.2; also elsewhere on the board
MOT1_IN1: U7.8 (BIN1/BPHASE), U7.10 (AIN1/APHASE); also elsewhere on the board
MOT1_IN2: U7.7 (BIN2/BENBL), U7.9 (AIN2/AENBL); also elsewhere on the board
MOT1_OUT1: J7.5, U7.2 (AOUT1), U7.4 (BOUT1)
MOT1_OUT2: J7.6, U7.3 (AOUT2), U7.5 (BOUT2)
MOT2_A: J8.3; also elsewhere on the board
MOT2_B: J8.2; also elsewhere on the board
MOT2_IN1: U8.8 (BIN1/BPHASE), U8.10 (AIN1/APHASE); also elsewhere on the board
MOT2_IN2: U8.7 (BIN2/BENBL), U8.9 (AIN2/AENBL); also elsewhere on the board
MOT2_OUT1: J8.5, U8.2 (AOUT1), U8.4 (BOUT1)
MOT2_OUT2: J8.6, U8.3 (AOUT2), U8.5 (BOUT2)
MOT3_A: J9.3; also elsewhere on the board
MOT3_B: J9.2; also elsewhere on the board
MOT3_IN1: U9.8 (BIN1/BPHASE), U9.10 (AIN1/APHASE); also elsewhere on the board
MOT3_IN2: U9.7 (BIN2/BENBL), U9.9 (AIN2/AENBL); also elsewhere on the board
MOT3_OUT1: J9.5, U9.2 (AOUT1), U9.4 (BOUT1)
MOT3_OUT2: J9.6, U9.3 (AOUT2), U9.5 (BOUT2)
MOT4_A: J10.3; also elsewhere on the board
MOT4_B: J10.2; also elsewhere on the board
MOT4_IN1: U10.8 (BIN1/BPHASE), U10.10 (AIN1/APHASE); also elsewhere on the board
MOT4_IN2: U10.7 (BIN2/BENBL), U10.9 (AIN2/AENBL); also elsewhere on the board
MOT4_OUT1: J10.5, U10.2 (AOUT1), U10.4 (BOUT1)
MOT4_OUT2: J10.6, U10.3 (AOUT2), U10.5 (BOUT2)
SUPPLY: C24.1, C25.1, C27.1, C28.1, C30.1, C31.1, C33.1, C34.1, U7.1 (VM), U8.1 (VM), U9.1 (VM), U10.1 (VM); also elsewhere on the board

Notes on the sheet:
left-back motor
right-front motor
right-back motor
left-front motor

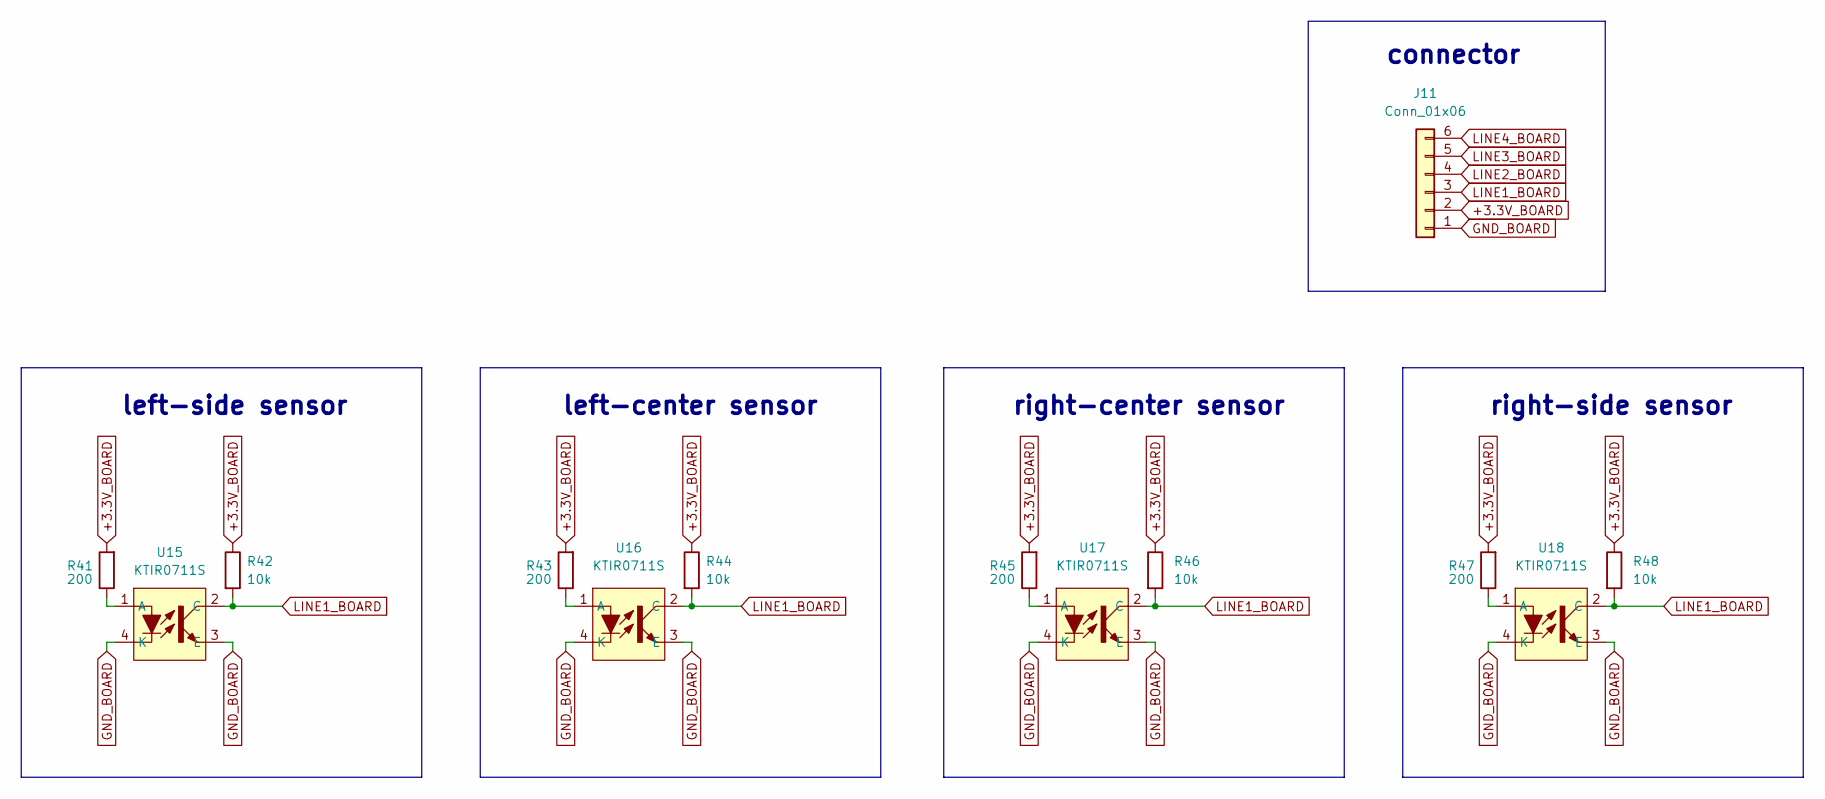
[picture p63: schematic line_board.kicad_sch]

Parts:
J11: Conn_01x06
R41, R43, R45, R47: 200
R42, R44, R46, R48: 10k
U15, U16, U17, U18: KTIR0711S

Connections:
+3.3V_BOARD: J11.2, R41.2, R42.1, R43.2, R44.1, R45.2, R46.1, R47.2, R48.1
GND_BOARD: J11.1, U15.3 (E), U15.4 (K), U16.3 (E), U16.4 (K), U17.3 (E), U17.4 (K), U18.3 (E), U18.4 (K)
LINE1_BOARD: J11.3, R42.2, R44.2, R46.2, R48.2, U15.2 (C), U16.2 (C), U17.2 (C), U18.2 (C)
LINE2_BOARD: J11.4
LINE3_BOARD: J11.5
LINE4_BOARD: J11.6
unnamed: R41.1, U15.1 (A)
unnamed: R43.1, U16.1 (A)
unnamed: R45.1, U17.1 (A)
unnamed: R47.1, U18.1 (A)

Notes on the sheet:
left-side sensor
right-center sensor
connector
right-side sensor
left-center sensor

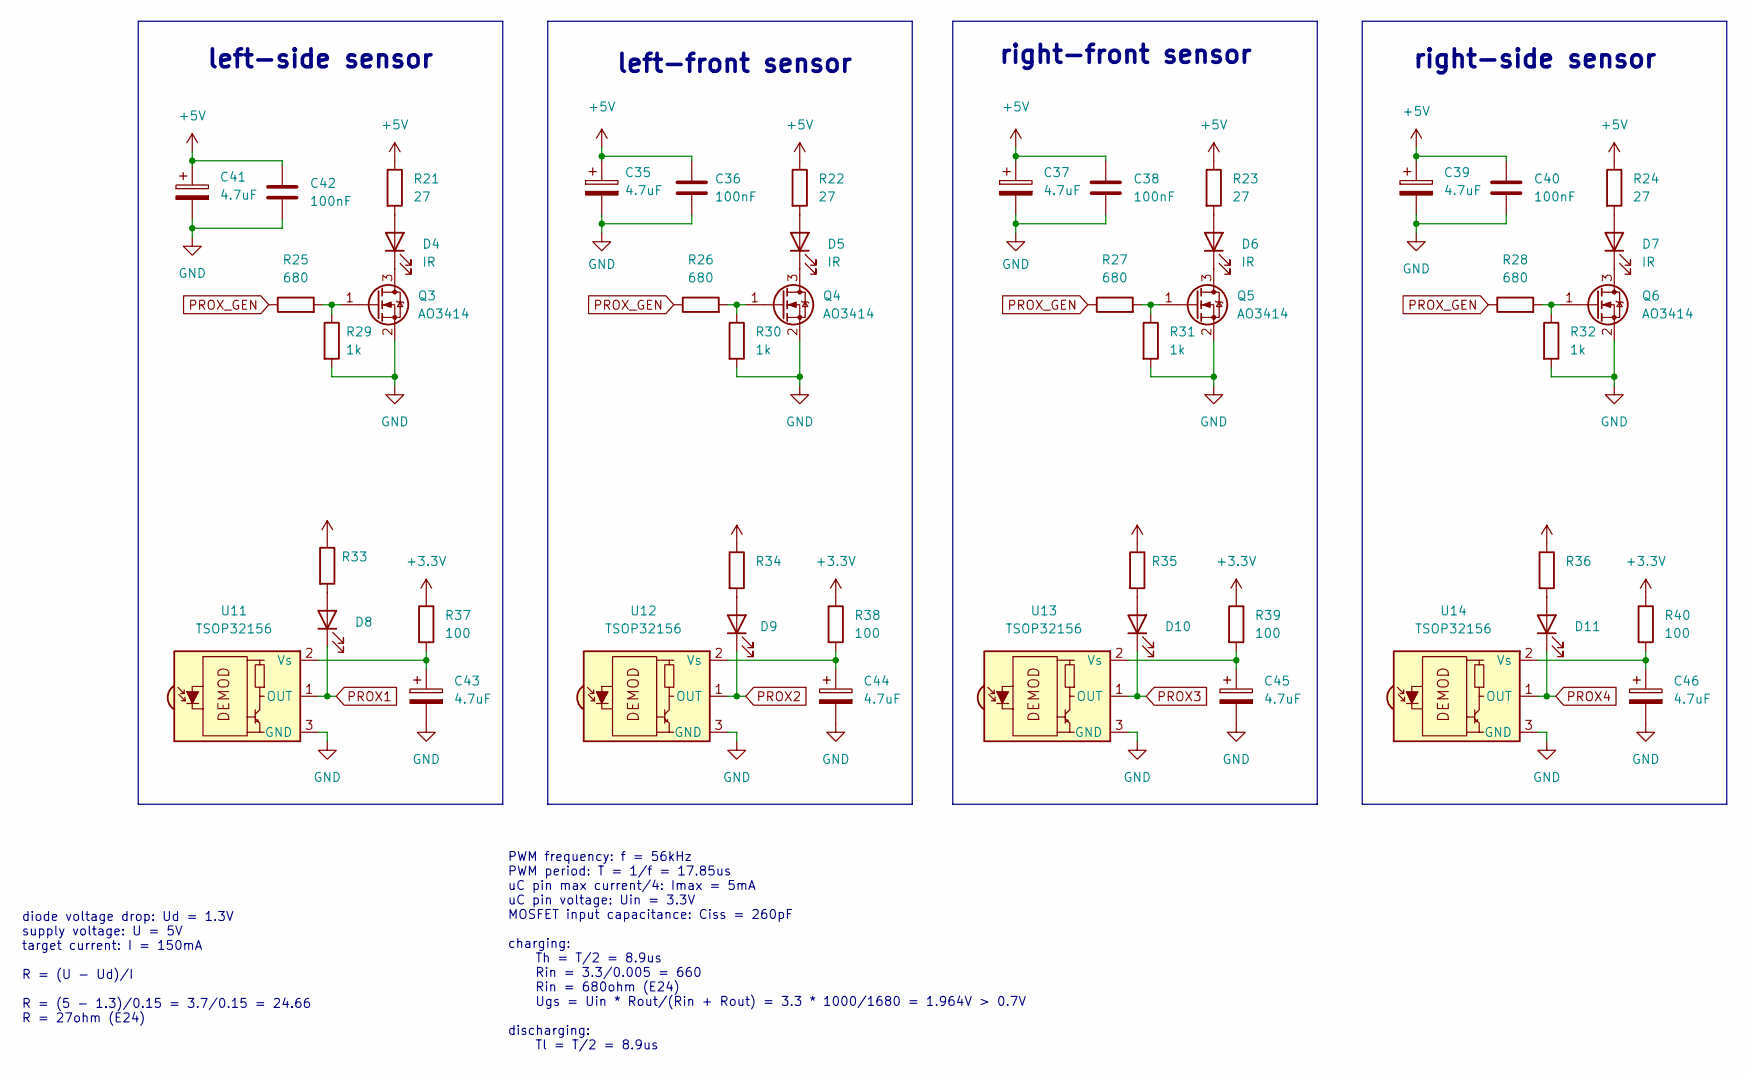
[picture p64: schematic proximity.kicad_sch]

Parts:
C35, C37, C39, C41, C43, C44, C45, C46: 4.7uF
C36, C38, C40, C42: 100nF
D4, D5, D6, D7: IR
D8, D9, D10, D11: (no value)
Q3, Q4, Q5, Q6: AO3414; SOT-23
R21, R22, R23, R24: 27
R25, R26, R27, R28: 680
R29, R30, R31, R32: 1k
R33, R34, R35, R36: (no value)
R37, R38, R39, R40: 100
U11, U12, U13, U14: TSOP32156; Vishay_MOLD-3Pin

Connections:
+5V: C35.1, C36.1, C37.1, C38.1, C39.1, C40.1, C41.1, C42.1, R21.1, R22.1, R23.1, R24.1; also elsewhere on the board
GND: C35.2, C36.2, C37.2, C38.2, C39.2, C40.2, C41.2, C42.2, C43.2, C44.2, C45.2, C46.2, Q3.2 (S), Q4.2 (S), Q5.2 (S), Q6.2 (S), R29.2, R30.2, R31.2, R32.2, U11.3 (GND), U12.3 (GND), U13.3 (GND), U14.3 (GND); also elsewhere on the board
unnamed: C43.1, R37.2, U11.2 (Vs)
unnamed: C44.1, R38.2, U12.2 (Vs)
unnamed: C45.1, R39.2, U13.2 (Vs)
unnamed: C46.1, R40.2, U14.2 (Vs)
unnamed: D4.1 (K), Q3.3 (D)
unnamed: D4.2 (A), R21.2
unnamed: D5.1 (K), Q4.3 (D)
unnamed: D5.2 (A), R22.2
unnamed: D6.1 (K), Q5.3 (D)
unnamed: D6.2 (A), R23.2
unnamed: D7.1 (K), Q6.3 (D)
unnamed: D7.2 (A), R24.2
unnamed: D8.2 (A), R33.2
unnamed: D9.2 (A), R34.2
unnamed: D10.2 (A), R35.2
unnamed: D11.2 (A), R36.2
unnamed: Q3.1 (G), R25.2, R29.1
unnamed: Q4.1 (G), R26.2, R30.1
unnamed: Q5.1 (G), R27.2, R31.1
unnamed: Q6.1 (G), R28.2, R32.1
PROX1: D8.1 (K), U11.1 (OUT); also elsewhere on the board
PROX2: D9.1 (K), U12.1 (OUT); also elsewhere on the board
PROX3: D10.1 (K), U13.1 (OUT); also elsewhere on the board
PROX4: D11.1 (K), U14.1 (OUT); also elsewhere on the board
PROX_GEN: R25.1, R26.1, R27.1, R28.1; also elsewhere on the board

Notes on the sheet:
left-side sensor
left-front sensor
right-side sensor
PWM frequency: f = 56kHz PWM period: T = 1/f = 17.85us uC pin max current/4: Imax = 5mA uC pin voltage: Uin = 3.3V MOSFET input capacitance: Ciss = 260pF charging: Th = T/2 = 8.9us Rin = 3.3/0.005 = 660 Rin = 680ohm (E24) Ugs = Uin * Rout/(Rin + Rout) = 3.3 * 1000/1680 = 1.964V > 0.7V discharging: 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
right-front sensor
diode voltage drop: Ud = 1.3V supply voltage: U = 5V target current: I = 150mA R = (U - Ud)/I R = (5 - 1.3)/0.15 = 3.7/0.15 = 24.66 R = 27ohm (E24)

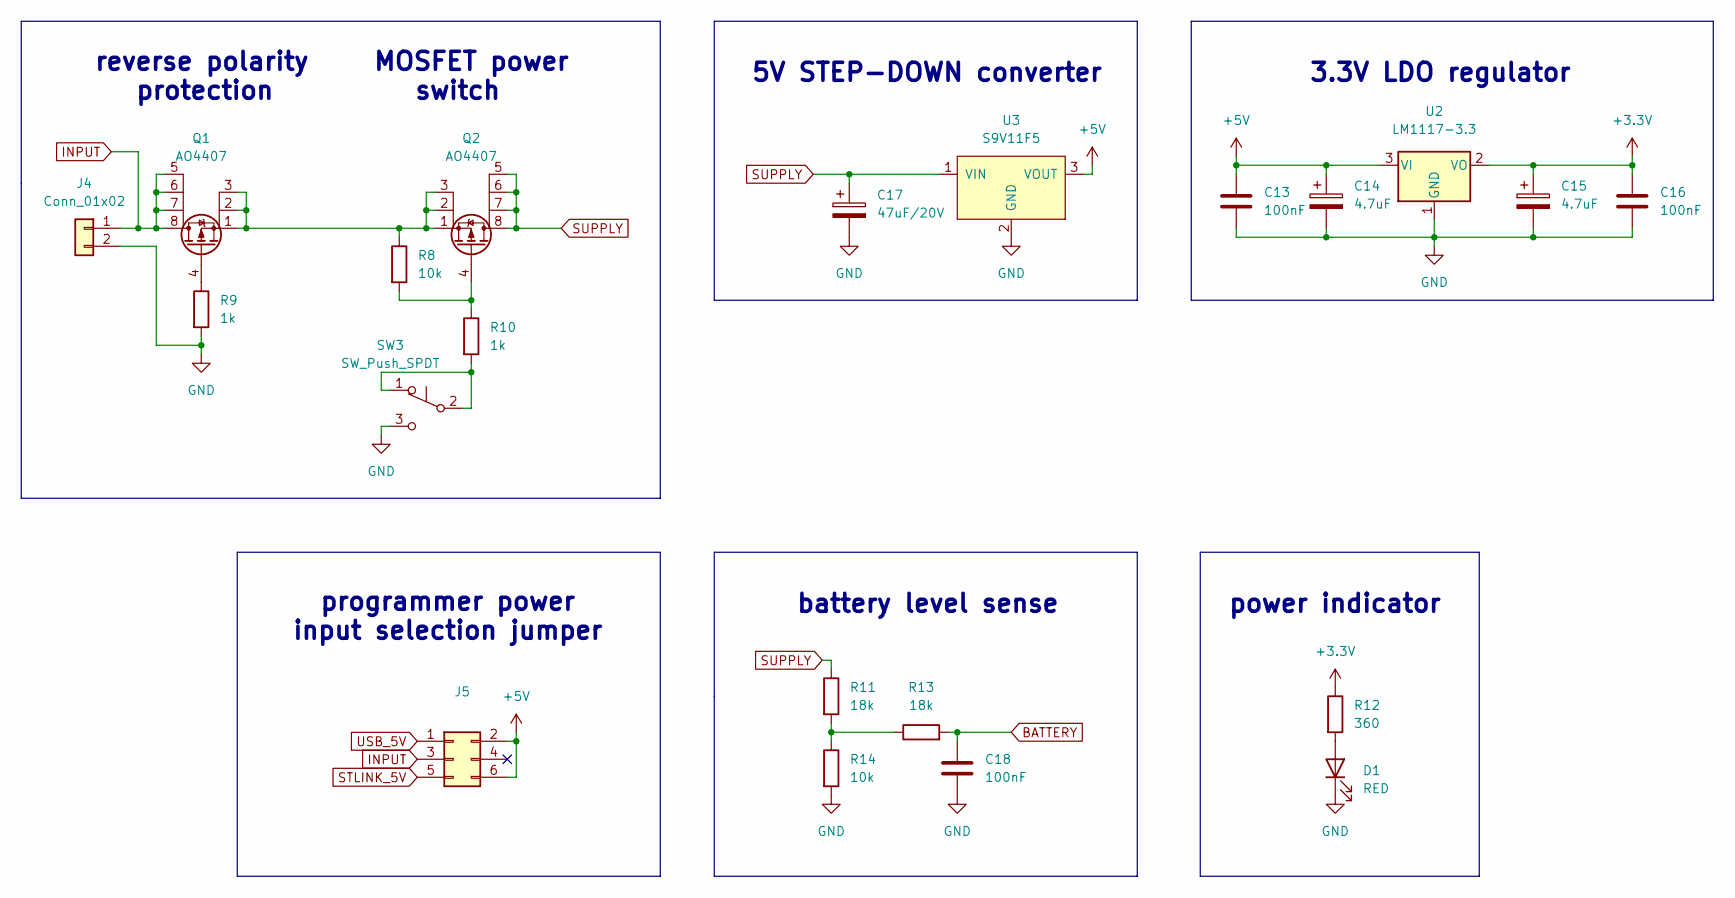
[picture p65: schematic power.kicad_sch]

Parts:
C13, C16, C18: 100nF
C14, C15: 4.7uF
C17: 47uF/20V
D1: RED
J4: Conn_01x02
J5: (no value)
Q1, Q2: AO4407
R8, R14: 10k
R9, R10: 1k
R11, R13: 18k
R12: 360
SW3: SW_Push_SPDT
U2: LM1117-3.3
U3: S9V11F5

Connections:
+5V: C13.1, C14.1, J5.2, J5.6, U2.3 (VI), U3.3 (VOUT); also elsewhere on the board
BATTERY: C18.1, R13.2; also elsewhere on the board
GND: C13.2, C14.2, C15.2, C16.2, C17.2, C18.2, D1.1 (K), J4.2, R9.2, R14.2, SW3.3 (C), U2.1 (GND), U3.2 (GND); also elsewhere on the board
INPUT: J4.1, J5.3, Q1.5, Q1.6, Q1.7, Q1.8
unnamed: D1.2 (A), R12.2
unnamed: Q1.1, Q1.2, Q1.3, Q2.1, Q2.2, Q2.3, R8.1
unnamed: Q1.4, R9.1
unnamed: Q2.4, R8.2, R10.1
unnamed: R10.2, SW3.1 (A), SW3.2 (B)
unnamed: R11.2, R13.1, R14.1
STLINK_5V: J5.5; also elsewhere on the board
SUPPLY: C17.1, Q2.5, Q2.6, Q2.7, Q2.8, R11.1, U3.1 (VIN); also elsewhere on the board
USB_5V: J5.1; also elsewhere on the board

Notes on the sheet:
battery level sense
MOSFET power switch
5V STEP-DOWN converter
programmer power input selection jumper
reverse polarity protection
power indicator
3.3V LDO regulator

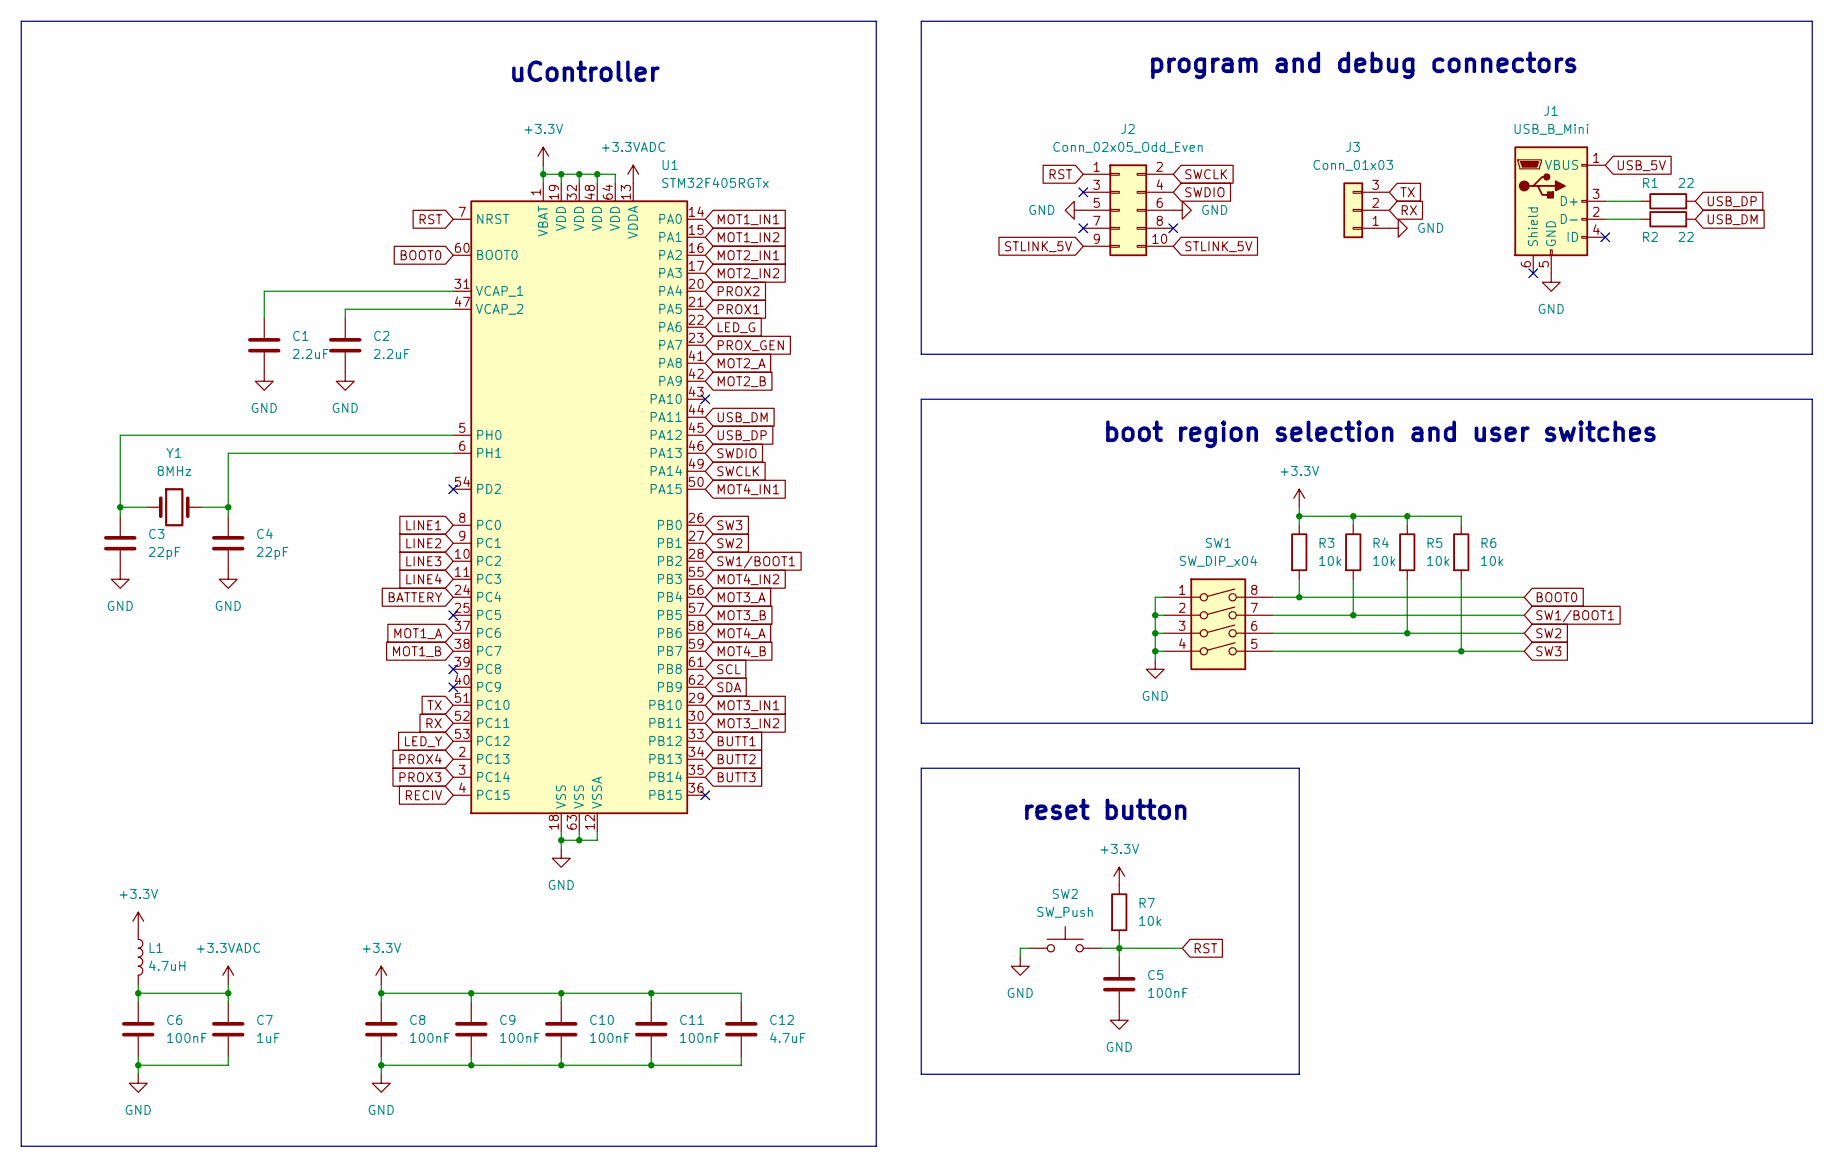
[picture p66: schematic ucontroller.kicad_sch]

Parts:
C1, C2: 2.2uF
C3, C4: 22pF
C5, C6, C8, C9, C10, C11: 100nF
C7: 1uF
C12: 4.7uF
J1: USB_B_Mini
J2: Conn_02x05_Odd_Even
J3: Conn_01x03
L1: 4.7uH
R1, R2: 22
R3, R4, R5, R6, R7: 10k
SW1: SW_DIP_x04
SW2: SW_Push
U1: STM32F405RGTx; LQFP-64_10x10mm_P0.5mm
Y1: 8MHz

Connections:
+3.3VADC: C6.1, C7.1, L1.2, U1.13 (VDDA)
BATTERY: U1.24 (PC4); also elsewhere on the board
BOOT0: R3.2, SW1.8, U1.60 (BOOT0)
BUTT1: U1.33 (PB12); also elsewhere on the board
BUTT2: U1.34 (PB13); also elsewhere on the board
BUTT3: U1.35 (PB14); also elsewhere on the board
GND: C1.2, C2.2, C3.2, C4.2, C5.2, C6.2, C7.2, C8.2, C9.2, C10.2, C11.2, C12.2, J1.5 (GND), J2.5, J2.6, J3.1, SW1.1, SW1.2, SW1.3, SW1.4, SW2.1, U1.12 (VSSA), U1.18 (VSS), U1.63 (VSS); also elsewhere on the board
LED_G: U1.22 (PA6); also elsewhere on the board
LED_Y: U1.53 (PC12); also elsewhere on the board
LINE1: U1.8 (PC0); also elsewhere on the board
LINE2: U1.9 (PC1); also elsewhere on the board
LINE3: U1.10 (PC2); also elsewhere on the board
LINE4: U1.11 (PC3); also elsewhere on the board
MOT1_A: U1.37 (PC6); also elsewhere on the board
MOT1_B: U1.38 (PC7); also elsewhere on the board
MOT1_IN1: U1.14 (PA0); also elsewhere on the board
MOT1_IN2: U1.15 (PA1); also elsewhere on the board
MOT2_A: U1.41 (PA8); also elsewhere on the board
MOT2_B: U1.42 (PA9); also elsewhere on the board
MOT2_IN1: U1.16 (PA2); also elsewhere on the board
MOT2_IN2: U1.17 (PA3); also elsewhere on the board
MOT3_A: U1.56 (PB4); also elsewhere on the board
MOT3_B: U1.57 (PB5); also elsewhere on the board
MOT3_IN1: U1.29 (PB10); also elsewhere on the board
MOT3_IN2: U1.30 (PB11); also elsewhere on the board
MOT4_A: U1.58 (PB6); also elsewhere on the board
MOT4_B: U1.59 (PB7); also elsewhere on the board
MOT4_IN1: U1.50 (PA15); also elsewhere on the board
MOT4_IN2: U1.55 (PB3); also elsewhere on the board
unnamed: C1.1, U1.31 (VCAP_1)
unnamed: C2.1, U1.47 (VCAP_2)
unnamed: C3.1, U1.5 (PH0), Y1.1
unnamed: C4.1, U1.6 (PH1), Y1.2
unnamed: J1.2 (D-), R2.1
unnamed: J1.3 (D+), R1.1
PROX1: U1.21 (PA5); also elsewhere on the board
PROX2: U1.20 (PA4); also elsewhere on the board
PROX3: U1.3 (PC14); also elsewhere on the board
PROX4: U1.2 (PC13); also elsewhere on the board
PROX_GEN: U1.23 (PA7); also elsewhere on the board
RECIV: U1.4 (PC15); also elsewhere on the board
RST: C5.1, J2.1, R7.2, SW2.2, U1.7 (NRST)
RX: J3.2, U1.52 (PC11)
SCL: U1.61 (PB8); also elsewhere on the board
SDA: U1.62 (PB9); also elsewhere on the board
STLINK_5V: J2.9, J2.10; also elsewhere on the board
SW1/BOOT1: R4.2, SW1.7, U1.28 (PB2)
SW2: R5.2, SW1.6, U1.27 (PB1)
SW3: R6.2, SW1.5, U1.26 (PB0)
SWCLK: J2.2, U1.49 (PA14)
SWDIO: J2.4, U1.46 (PA13)
TX: J3.3, U1.51 (PC10)
USB_5V: J1.1 (VBUS); also elsewhere on the board
USB_DM: R2.2, U1.44 (PA11)
USB_DP: R1.2, U1.45 (PA12)

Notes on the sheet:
uController
reset button
program and debug connectors
boot region selection and user switches

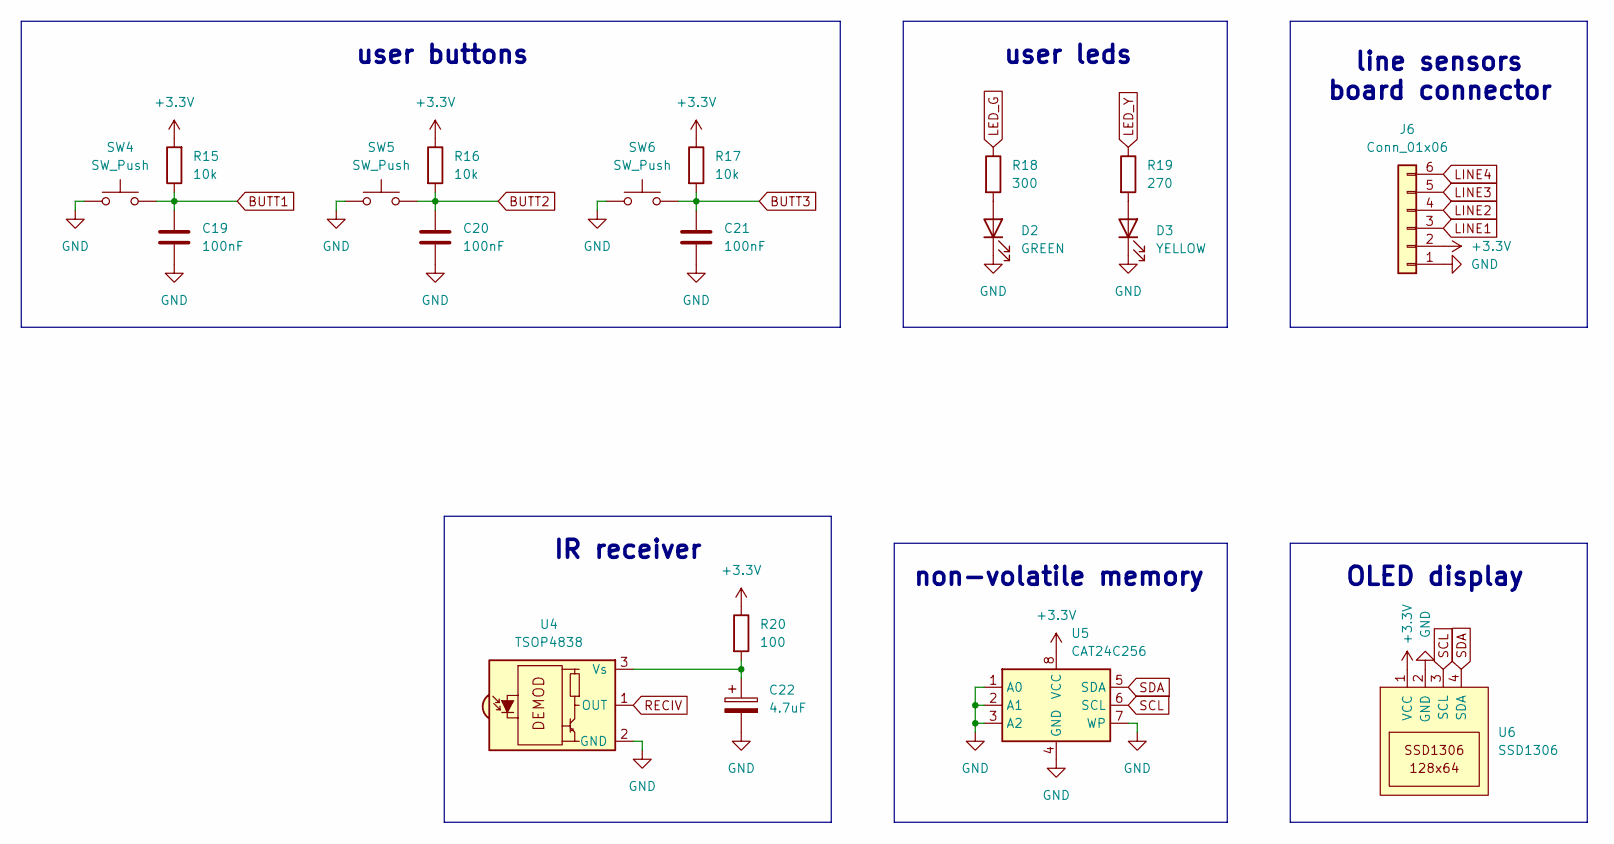
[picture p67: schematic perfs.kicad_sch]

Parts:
C19, C20, C21: 100nF
C22: 4.7uF
D2: GREEN
D3: YELLOW
J6: Conn_01x06
R15, R16, R17: 10k
R18: 300
R19: 270
R20: 100
SW4, SW5, SW6: SW_Push
U4: TSOP4838
U5: CAT24C256
U6: SSD1306

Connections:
BUTT1: C19.1, R15.1, SW4.2; also elsewhere on the board
BUTT2: C20.1, R16.2, SW5.2; also elsewhere on the board
BUTT3: C21.1, R17.2, SW6.2; also elsewhere on the board
GND: C19.2, C20.2, C21.2, C22.2, D2.1 (K), D3.1 (K), J6.1, SW4.1, SW5.1, SW6.1, U4.2 (GND), U5.1 (A0), U5.2 (A1), U5.3 (A2), U5.4 (GND), U5.7 (WP), U6.2 (GND); also elsewhere on the board
LED_G: R18.1; also elsewhere on the board
LED_Y: R19.1; also elsewhere on the board
LINE1: J6.3; also elsewhere on the board
LINE2: J6.4; also elsewhere on the board
LINE3: J6.5; also elsewhere on the board
LINE4: J6.6; also elsewhere on the board
unnamed: C22.1, R20.2, U4.3 (Vs)
unnamed: D2.2 (A), R18.2
unnamed: D3.2 (A), R19.2
RECIV: U4.1 (OUT); also elsewhere on the board
SCL: U5.6 (SCL), U6.3 (SCL); also elsewhere on the board
SDA: U5.5 (SDA), U6.4 (SDA); also elsewhere on the board

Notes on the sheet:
OLED display
non-volatile memory
IR receiver
user buttons
user leds
line sensors board connector

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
Board: 2 copper layers, 144 parts (11 on the bottom side), 98 nets, no tracks yet.

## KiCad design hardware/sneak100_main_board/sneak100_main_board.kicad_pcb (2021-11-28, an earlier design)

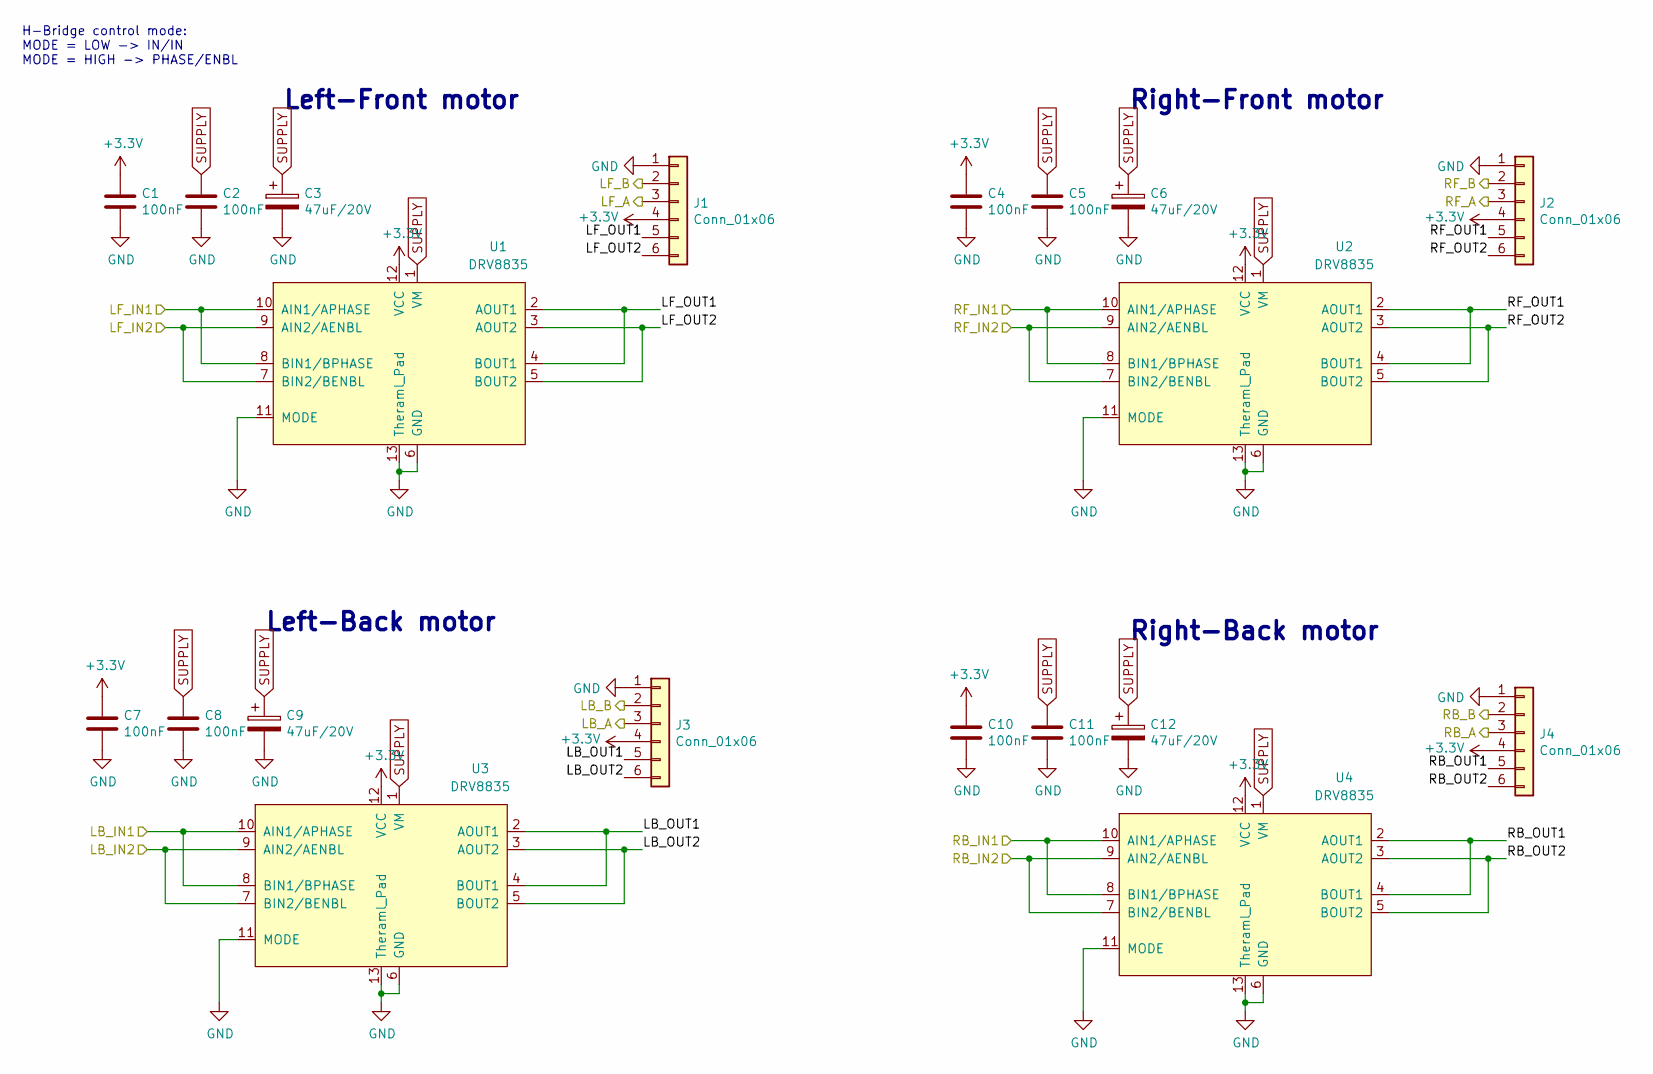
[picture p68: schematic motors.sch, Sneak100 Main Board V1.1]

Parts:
C1, C2, C4, C5, C7, C8, C10, C11: 100nF; C_0603_1608Metric
C3, C6, C9, C12: 47uF/20V; CP_EIA-7343-31_Kemet-D
J1, J2, J3, J4: Conn_01x06; PinSocket_1x06_P2.54mm_Horizontal
U1, U2, U3, U4: DRV8835; DRV8835_hand_solder

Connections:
+3V3: C1.1, C4.1, C7.1, C10.1, J1.4, J2.4, J3.4, J4.4, U1.12 (VCC), U2.12 (VCC), U3.12 (VCC), U4.12 (VCC); also elsewhere on the board
/controller/LB_A: J3.3; also elsewhere on the board
/controller/LB_B: J3.2; also elsewhere on the board
/controller/LB_IN1: U3.8 (BIN1/BPHASE), U3.10 (AIN1/APHASE); also elsewhere on the board
/controller/LB_IN2: U3.7 (BIN2/BENBL), U3.9 (AIN2/AENBL); also elsewhere on the board
/controller/LF_A: J1.3; also elsewhere on the board
/controller/LF_B: J1.2; also elsewhere on the board
/controller/LF_IN1: U1.8 (BIN1/BPHASE), U1.10 (AIN1/APHASE); also elsewhere on the board
/controller/LF_IN2: U1.7 (BIN2/BENBL), U1.9 (AIN2/AENBL); also elsewhere on the board
/controller/RB_A: J4.3; also elsewhere on the board
/controller/RB_B: J4.2; also elsewhere on the board
/controller/RB_IN1: U4.8 (BIN1/BPHASE), U4.10 (AIN1/APHASE); also elsewhere on the board
/controller/RB_IN2: U4.7 (BIN2/BENBL), U4.9 (AIN2/AENBL); also elsewhere on the board
/controller/RF_A: J2.3; also elsewhere on the board
/controller/RF_B: J2.2; also elsewhere on the board
/controller/RF_IN1: U2.8 (BIN1/BPHASE), U2.10 (AIN1/APHASE); also elsewhere on the board
/controller/RF_IN2: U2.7 (BIN2/BENBL), U2.9 (AIN2/AENBL); also elsewhere on the board
/motors/LB_OUT1: J3.5, U3.2 (AOUT1), U3.4 (BOUT1)
/motors/LB_OUT2: J3.6, U3.3 (AOUT2), U3.5 (BOUT2)
/motors/LF_OUT1: J1.5, U1.2 (AOUT1), U1.4 (BOUT1)
/motors/LF_OUT2: J1.6, U1.3 (AOUT2), U1.5 (BOUT2)
/motors/RB_OUT1: J4.5, U4.2 (AOUT1), U4.4 (BOUT1)
/motors/RB_OUT2: J4.6, U4.3 (AOUT2), U4.5 (BOUT2)
/motors/RF_OUT1: J2.5, U2.2 (AOUT1), U2.4 (BOUT1)
/motors/RF_OUT2: J2.6, U2.3 (AOUT2), U2.5 (BOUT2)
GND: C1.2, C2.2, C3.2, C4.2, C5.2, C6.2, C7.2, C8.2, C9.2, C10.2, C11.2, C12.2, J1.1, J2.1, J3.1, J4.1, U1.6 (GND), U1.11 (MODE), U1.13 (Theraml_Pad), U2.6 (GND), U2.11 (MODE), U2.13 (Theraml_Pad), U3.6 (GND), U3.11 (MODE), U3.13 (Theraml_Pad), U4.6 (GND), U4.11 (MODE), U4.13 (Theraml_Pad); also elsewhere on the board
SUPPLY: C2.1, C3.1, C5.1, C6.1, C8.1, C9.1, C11.1, C12.1, U1.1 (VM), U2.1 (VM), U3.1 (VM), U4.1 (VM); also elsewhere on the board

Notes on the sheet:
H-Bridge control mode: MODE = LOW -> IN/IN MODE = HIGH -> PHASE/ENBL
Left-Front motor
Right-Front motor
Left-Back motor
Right-Back motor

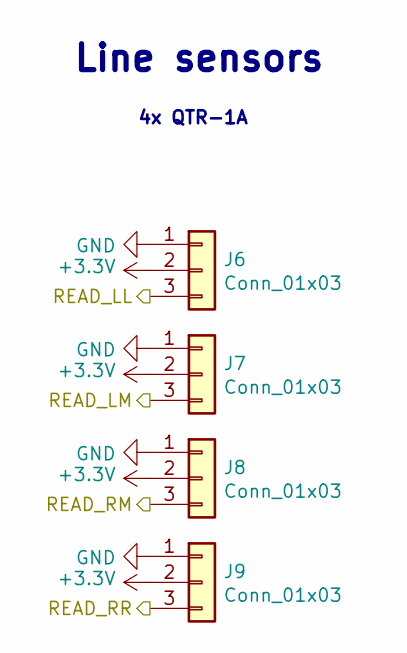
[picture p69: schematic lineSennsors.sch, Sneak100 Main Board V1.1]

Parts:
J6, J7, J8, J9: Conn_01x03; PinSocket_1x03_P2.54mm_Vertical

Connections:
+3V3: J6.2, J7.2, J8.2, J9.2; also elsewhere on the board
/controller/LINE_LL: J6.3; also elsewhere on the board
/controller/LINE_LM: J7.3; also elsewhere on the board
/controller/LINE_RM: J8.3; also elsewhere on the board
/controller/LINE_RR: J9.3; also elsewhere on the board
GND: J6.1, J7.1, J8.1, J9.1; also elsewhere on the board

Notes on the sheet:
Line sensors
4x QTR-1A

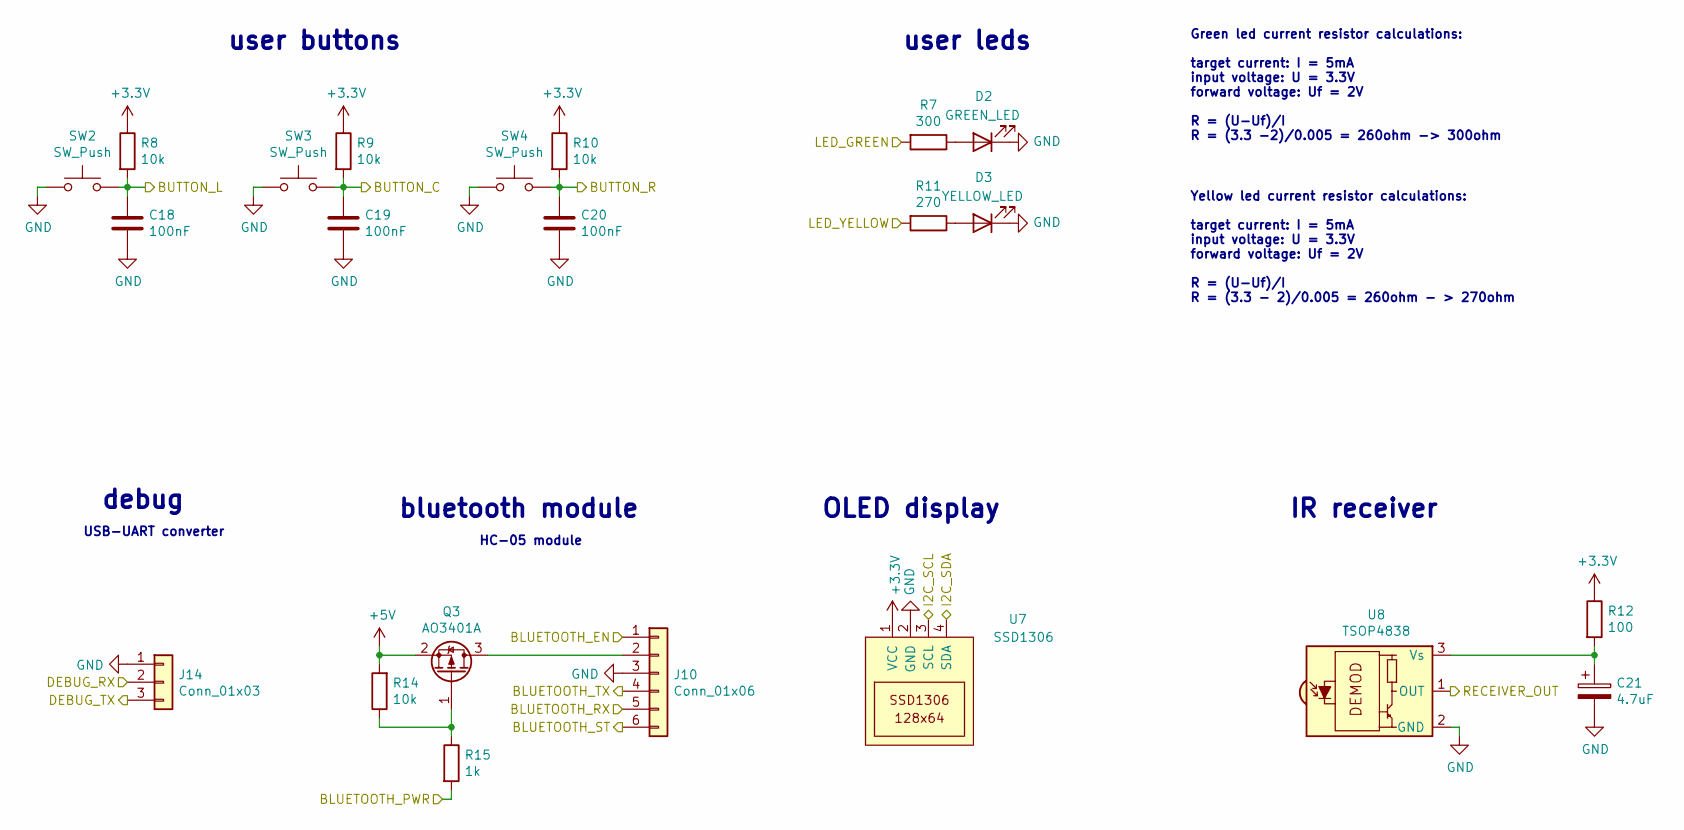
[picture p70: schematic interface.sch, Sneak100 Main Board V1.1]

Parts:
C18, C19, C20: 100nF; C_0603_1608Metric
C21: 4.7uF; CP_EIA-3216-18_Kemet-A
D2: GREEN_LED; LED_0603_1608Metric
D3: YELLOW_LED; LED_0603_1608Metric
J10: Conn_01x06; PinSocket_1x06_P2.54mm_Vertical
J14: Conn_01x03; PinSocket_1x03_P2.54mm_Vertical
Q3: AO3401A; SOT-23
R7: 300; R_0603_1608Metric
R8, R9, R10, R14: 10k; R_0603_1608Metric
R11: 270; R_0603_1608Metric
R12: 100; R_0603_1608Metric
R15: 1k; R_0603_1608Metric
SW2, SW3, SW4: SW_Push; SW_Push_1P1T_NO_6x6mm_H9.5mm
U7: SSD1306; SSD1306_module_screw
U8: TSOP4838; PinHeader_1x03_P2.54mm_Vertical

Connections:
+3V3: R8.1, R9.1, R10.1, R12.1, U7.1 (VCC); also elsewhere on the board
+5V: Q3.2 (S), R14.2; also elsewhere on the board
/controller/BLUETOOTH_EN: J10.1; also elsewhere on the board
/controller/BLUETOOTH_PWR: R15.2; also elsewhere on the board
/controller/BLUETOOTH_ST: J10.6; also elsewhere on the board
/controller/I2C1_SCL: U7.3 (SCL); also elsewhere on the board
/controller/I2C1_SDA: U7.4 (SDA); also elsewhere on the board
/controller/RECEIVER_OUT: U8.1 (OUT); also elsewhere on the board
/interface/BLUETOOTH_RX: J10.5; also elsewhere on the board
/interface/BLUETOOTH_TX: J10.4; also elsewhere on the board
/interface/BUTTON_C: C19.1, R9.2, SW3.2; also elsewhere on the board
/interface/BUTTON_L: C18.1, R8.2, SW2.2; also elsewhere on the board
/interface/BUTTON_R: C20.1, R10.2, SW4.2; also elsewhere on the board
/interface/DEBUG_RX: J14.2; also elsewhere on the board
/interface/DEBUG_TX: J14.3; also elsewhere on the board
/interface/LED_GREEN: R7.2; also elsewhere on the board
/interface/LED_YELLOW: R11.2; also elsewhere on the board
GND: C18.2, C19.2, C20.2, C21.2, D2.1 (K), D3.1 (K), J10.3, J14.1, SW2.1, SW3.1, SW4.1, U7.2 (GND), U8.2 (GND); also elsewhere on the board
unnamed: C21.1, R12.2, U8.3 (Vs)
unnamed: D2.2 (A), R7.1
unnamed: D3.2 (A), R11.1
unnamed: J10.2, Q3.3 (D)
unnamed: Q3.1 (G), R14.1, R15.1

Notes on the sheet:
Green led current resistor calculations: target current: I = 5mA input voltage: U = 3.3V forward voltage: Uf = 2V R = (U-Uf)/I R = (3.3 -2)/0.005 = 260ohm -> 300ohm
user buttons
user leds
bluetooth module
OLED display
IR receiver
Yellow led current resistor calculations: target current: I = 5mA input voltage: U = 3.3V forward voltage: Uf = 2V R = (U-Uf)/I R = (3.3 - 2)/0.005 = 260ohm - > 270ohm
HC-05 module
debug
USB-UART converter

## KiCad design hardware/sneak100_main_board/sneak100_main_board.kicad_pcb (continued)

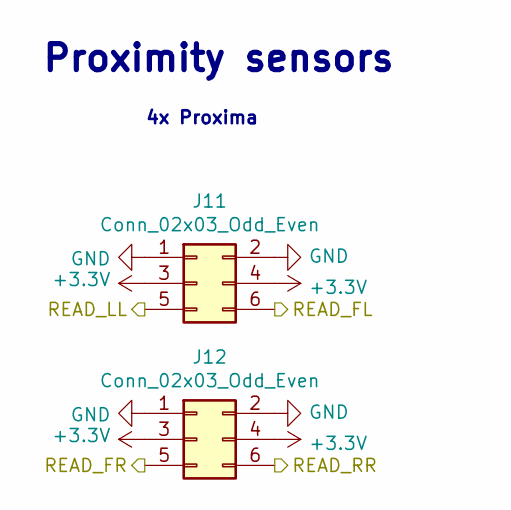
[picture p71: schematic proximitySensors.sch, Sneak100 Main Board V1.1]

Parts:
J11, J12: Conn_02x03_Odd_Even; PinSocket_2x03_P2.54mm_Horizontal

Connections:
+3V3: J11.3, J11.4, J12.3, J12.4; also elsewhere on the board
/controller/PROXIMITY_FL: J11.6; also elsewhere on the board
/controller/PROXIMITY_FR: J12.5; also elsewhere on the board
/controller/PROXIMITY_LL: J11.5; also elsewhere on the board
/controller/PROXIMITY_RR: J12.6; also elsewhere on the board
GND: J11.1, J11.2, J12.1, J12.2; also elsewhere on the board

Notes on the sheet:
Proximity sensors
4x Proxima

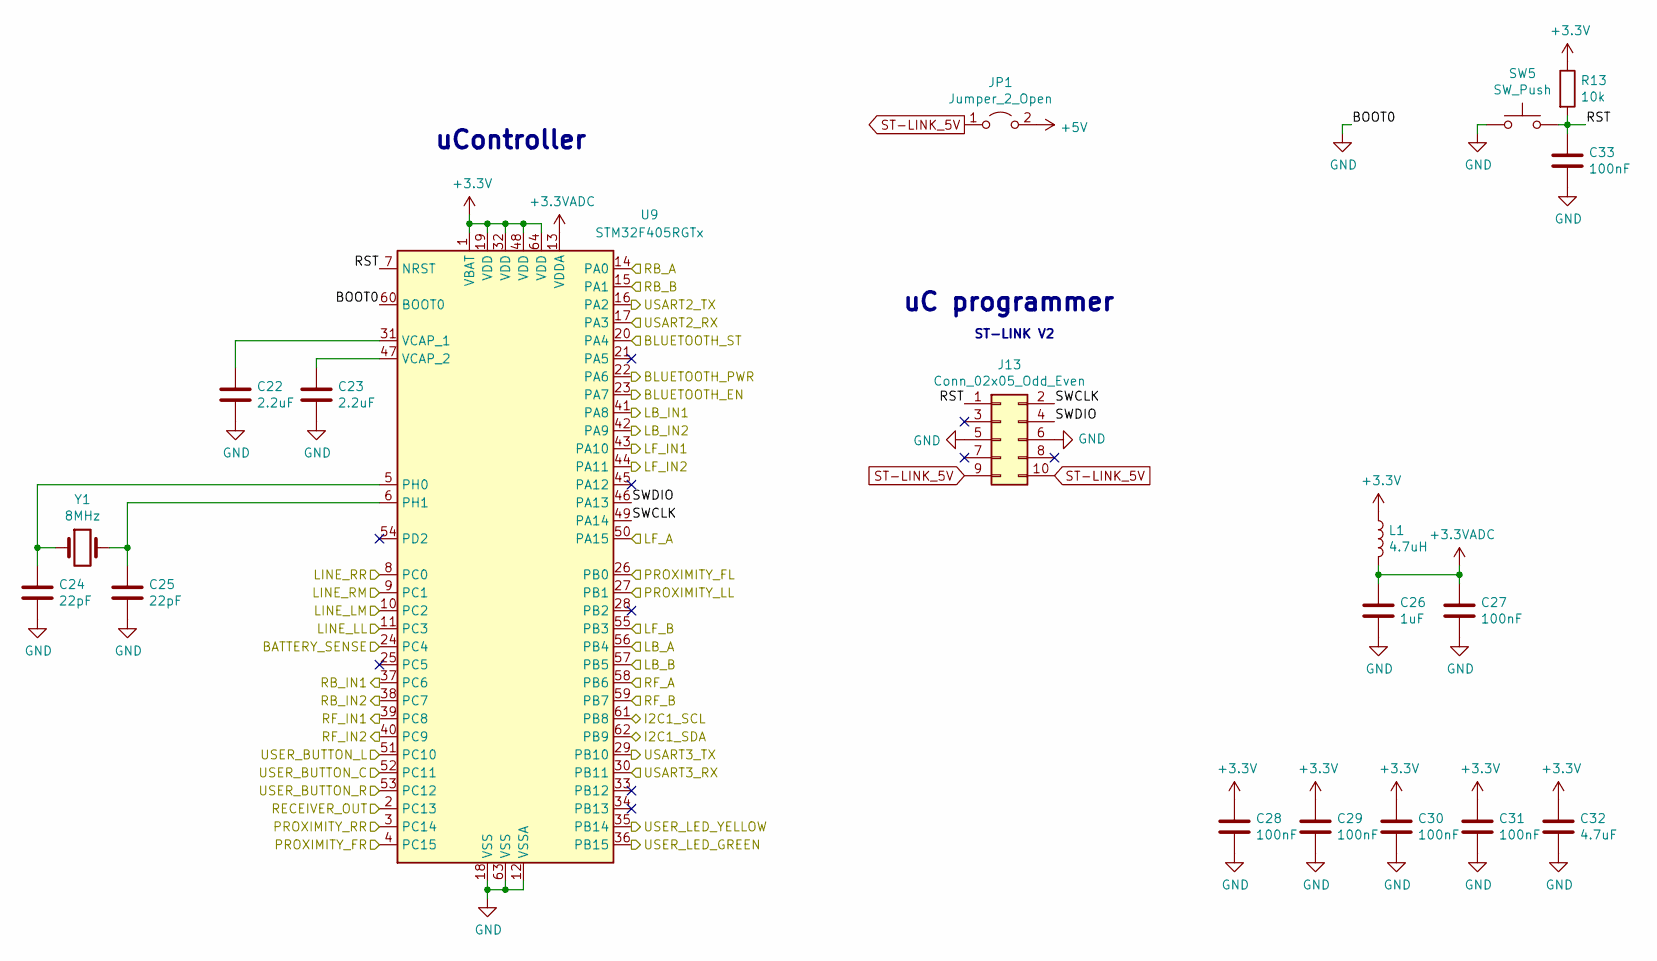
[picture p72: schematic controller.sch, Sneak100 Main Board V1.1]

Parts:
C22, C23: 2.2uF; C_0603_1608Metric
C24, C25: 22pF; C_0603_1608Metric
C26: 1uF; C_0603_1608Metric
C27, C28, C29, C30, C31, C33: 100nF; C_0603_1608Metric
C32: 4.7uF; C_0603_1608Metric
J13: Conn_02x05_Odd_Even; IDC-Header_2x05_P2.54mm_Vertical
JP1: Jumper_2_Open; PinHeader_1x03_P2.54mm_Vertical
L1: 4.7uH; L_0805_2012Metric
R13: 10k; R_0603_1608Metric
SW5: SW_Push; SW_Push_1P1T_NO_6x6mm_H9.5mm
U9: STM32F405RGTx; LQFP-64_10x10mm_P0.5mm
Y1: 8MHz; Crystal_SMD_5032-2Pin_5.0x3.2mm

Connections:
+3.3VADC: C26.1, C27.1, L1.2, U9.13 (VDDA)
+3V3: C28.1, C29.1, C30.1, C31.1, C32.1, L1.1, R13.1, U9.1 (VBAT), U9.19 (VDD), U9.32 (VDD), U9.48 (VDD), U9.64 (VDD); also elsewhere on the board
+5V: JP1.2 (B); also elsewhere on the board
/controller/BATTERY_SENSE: U9.24 (PC4); also elsewhere on the board
/controller/BLUETOOTH_EN: U9.23 (PA7); also elsewhere on the board
/controller/BLUETOOTH_PWR: U9.22 (PA6); also elsewhere on the board
/controller/BLUETOOTH_ST: U9.20 (PA4); also elsewhere on the board
/controller/I2C1_SCL: U9.61 (PB8); also elsewhere on the board
/controller/I2C1_SDA: U9.62 (PB9); also elsewhere on the board
/controller/LB_A: U9.56 (PB4); also elsewhere on the board
/controller/LB_B: U9.57 (PB5); also elsewhere on the board
/controller/LB_IN1: U9.41 (PA8); also elsewhere on the board
/controller/LB_IN2: U9.42 (PA9); also elsewhere on the board
/controller/LF_A: U9.50 (PA15); also elsewhere on the board
/controller/LF_B: U9.55 (PB3); also elsewhere on the board
/controller/LF_IN1: U9.43 (PA10); also elsewhere on the board
/controller/LF_IN2: U9.44 (PA11); also elsewhere on the board
/controller/LINE_LL: U9.11 (PC3); also elsewhere on the board
/controller/LINE_LM: U9.10 (PC2); also elsewhere on the board
/controller/LINE_RM: U9.9 (PC1); also elsewhere on the board
/controller/LINE_RR: U9.8 (PC0); also elsewhere on the board
/controller/PROXIMITY_FL: U9.26 (PB0); also elsewhere on the board
/controller/PROXIMITY_FR: U9.4 (PC15); also elsewhere on the board
/controller/PROXIMITY_LL: U9.27 (PB1); also elsewhere on the board
/controller/PROXIMITY_RR: U9.3 (PC14); also elsewhere on the board
/controller/RB_A: U9.14 (PA0); also elsewhere on the board
/controller/RB_B: U9.15 (PA1); also elsewhere on the board
/controller/RB_IN1: U9.37 (PC6); also elsewhere on the board
/controller/RB_IN2: U9.38 (PC7); also elsewhere on the board
/controller/RECEIVER_OUT: U9.2 (PC13); also elsewhere on the board
/controller/RF_A: U9.58 (PB6); also elsewhere on the board
/controller/RF_B: U9.59 (PB7); also elsewhere on the board
/controller/RF_IN1: U9.39 (PC8); also elsewhere on the board
/controller/RF_IN2: U9.40 (PC9); also elsewhere on the board
/controller/RST: C33.1, J13.1, R13.2, SW5.2, U9.7 (NRST)
/controller/SWCLK: J13.2, U9.49 (PA14)
/controller/SWDIO: J13.4, U9.46 (PA13)
/interface/BLUETOOTH_RX: U9.16 (PA2); also elsewhere on the board
/interface/BLUETOOTH_TX: U9.17 (PA3); also elsewhere on the board
/interface/BUTTON_C: U9.52 (PC11); also elsewhere on the board
/interface/BUTTON_L: U9.51 (PC10); also elsewhere on the board
/interface/BUTTON_R: U9.53 (PC12); also elsewhere on the board
/interface/DEBUG_RX: U9.30 (PB11); also elsewhere on the board
/interface/DEBUG_TX: U9.29 (PB10); also elsewhere on the board
/interface/LED_GREEN: U9.36 (PB15); also elsewhere on the board
/interface/LED_YELLOW: U9.35 (PB14); also elsewhere on the board
GND: C22.2, C23.2, C24.2, C25.2, C26.2, C27.2, C28.2, C29.2, C30.2, C31.2, C32.2, C33.2, J13.5, J13.6, SW5.1, U9.12 (VSSA), U9.18 (VSS), U9.60 (BOOT0), U9.63 (VSS); also elsewhere on the board
unnamed: C22.1, U9.31 (VCAP_1)
unnamed: C23.1, U9.47 (VCAP_2)
unnamed: C24.1, U9.5 (PH0), Y1.1
unnamed: C25.1, U9.6 (PH1), Y1.2
ST-LINK_5V: J13.9, J13.10, JP1.1 (A)

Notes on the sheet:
uController
uC programmer
ST-LINK V2

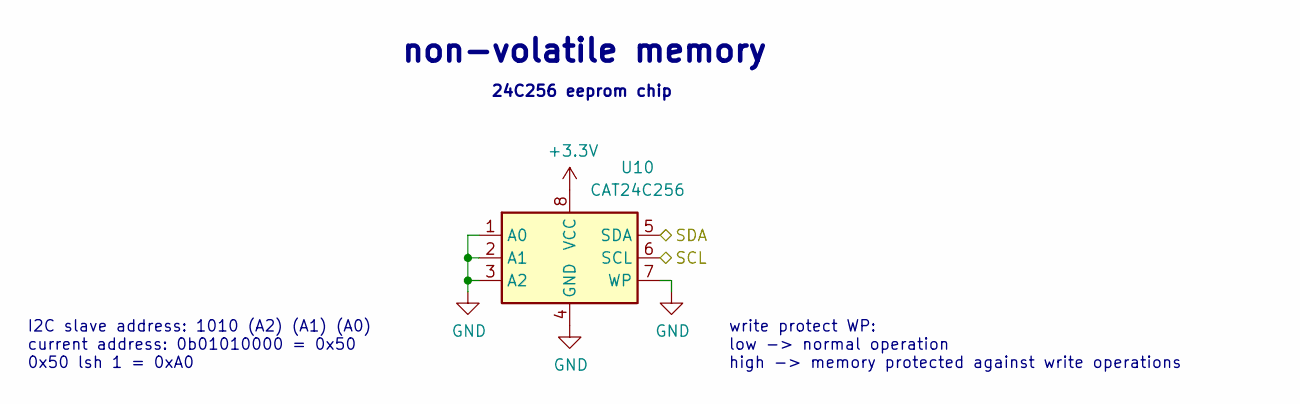
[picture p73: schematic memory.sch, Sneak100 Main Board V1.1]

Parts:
U10: CAT24C256; SOIC-8_3.9x4.9mm_P1.27mm

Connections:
+3V3: U10.8 (VCC); also elsewhere on the board
/controller/I2C1_SCL: U10.6 (SCL); also elsewhere on the board
/controller/I2C1_SDA: U10.5 (SDA); also elsewhere on the board
GND: U10.1 (A0), U10.2 (A1), U10.3 (A2), U10.4 (GND), U10.7 (WP); also elsewhere on the board

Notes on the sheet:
I2C slave address: 1010 (A2) (A1) (A0) current address: 0b01010000 = 0x50 0x50 lsh 1 = 0xA0
write protect WP: low -> normal operation high -> memory protected against write operations
non-volatile memory
24C256 eeprom chip


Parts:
C13: 47uF/20V; CP_EIA-7343-31_Kemet-D
C14, C17: 100nF; C_0603_1608Metric
C15, C16: 4.7uF; CP_EIA-3216-18_Kemet-A
D1: RED_LED; LED_0603_1608Metric
J5: Conn_01x02; PinHeader_1x02_P2.54mm_Horizontal
Q1, Q2: AO4407; SOIC-8_3.9x4.9mm_P1.27mm
R1, R6: 10k; R_0603_1608Metric
R2, R3: 1k; R_0603_1608Metric
R4: 18k; R_0603_1608Metric
R5: 360; R_0603_1608Metric
SW1: SW_Push_SPDT; ESP2010_90
U5: LM1117-3.3; SOT-223-3_TabPin2
U6: S9V11F5; S9V11F5_module

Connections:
+3V3: C16.1, C17.1, R5.1, U5.2 (VO); also elsewhere on the board
+5V: C14.1, C15.1, U5.3 (VI), U6.3 (VOUT); also elsewhere on the board
/controller/BATTERY_SENSE: R4.2, R6.1; also elsewhere on the board
GND: C13.2, C14.2, C15.2, C16.2, C17.2, D1.1 (K), J5.1, R2.2, R6.2, SW1.3 (C), U5.1 (GND), U6.2 (GND); also elsewhere on the board
unnamed: D1.2 (A), R5.2
unnamed: J5.2, Q1.5, Q1.6, Q1.7, Q1.8
unnamed: Q1.1, Q1.2, Q1.3, Q2.1, Q2.2, Q2.3, R1.1
unnamed: Q1.4, R2.1
unnamed: Q2.4, R1.2, R3.1
unnamed: R3.2, SW1.1 (A), SW1.2 (B)
SUPPLY: C13.1, Q2.5, Q2.6, Q2.7, Q2.8, R4.1, U6.1 (VIN); also elsewhere on the board

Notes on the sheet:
5V step-down converter
Battery level sense
Power level indicator
Power input menagement
3.3V LDO regulator
Voltage divider calculations: U_in max = 8.4V U_out max = 3V U_out = U_in * R2/(R1+R2) U_out * (R1+R2) = U_in * R2 U_out * R1+ U_out * R2 = U_in * R2 U_out * R1 = (U_in - U_out) * R2 R1 = R2 * (U_in - U_out)/U_out assume R2 = 10k R1 = 10000 * (8.4 - 3)/3 = 18 kohm
Power red led current resistor calculations: target current: I = 5mA input voltage: U1= 3.3V forward voltage: Uf = 1.6V R = (U-Uf)/I R_3.3V = (3.3 -1.6)/0.005 = 340 ohm -> 360 ohm



Board: 2 copper layers, 68.0 x 75.0 mm, 86 parts (10 on the bottom side), 72 nets.

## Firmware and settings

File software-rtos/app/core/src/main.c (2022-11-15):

#include "stm32f4xx.h"
#include "FreeRTOS.h"
#include "task.h"

#include "adc.h"
#include "i2c1.h"
#include "uart2.h"
#include "uart3.h"

#include "cli.h"
#include "gui.h"
#include "motors.h"
#include "periph.h"
#include "display.h"
#include "rc5.h"

#include "robot.h"

void vApplicationStackOverflowHook(TaskHandle_t pxTask, char *pcTaskName) {
	(void)pcTaskName;
	(void)pxTask;

	taskDISABLE_INTERRUPTS();
	while(1);
}

void vApplicationGetIdleTaskMemory(StaticTask_t **ppxIdleTaskTCBBuffer, StackType_t **ppxIdleTaskStackBuffer, uint32_t *pulIdleTaskStackSize) {
    static StaticTask_t xIdleTaskTCB;
    static StackType_t uxIdleTaskStack[configMINIMAL_STACK_SIZE];

    *ppxIdleTaskTCBBuffer = &xIdleTaskTCB;
    *ppxIdleTaskStackBuffer = uxIdleTaskStack;
    *pulIdleTaskStackSize = configMINIMAL_STACK_SIZE;
}

void vApplicationMallocFailedHook() {
	while(1);
}

void clock_init() {
	RCC->CR |=RCC_CR_HSEON;
    while(!(RCC->CR & RCC_CR_HSERDY));

    RCC->APB1ENR |=RCC_APB1ENR_PWREN;
    PWR->CR |=(3<<PWR_CR_VOS_Pos);
    FLASH->ACR |=FLASH_ACR_LATENCY_3WS | FLASH_ACR_PRFTEN | FLASH_ACR_ICEN | FLASH_ACR_DCEN;

    RCC->CFGR |=RCC_CFGR_PPRE1_DIV4 | RCC_CFGR_PPRE2_DIV2 | RCC_CFGR_HPRE_DIV1;
    
    RCC->PLLCFGR &=~(0x03F<<RCC_PLLCFGR_PLLM_Pos);
    RCC->PLLCFGR &=~(0x1FF<<RCC_PLLCFGR_PLLN_Pos);
    RCC->PLLCFGR &=~(0x003<<RCC_PLLCFGR_PLLP_Pos);
    RCC->PLLCFGR &=~(0x00F<<RCC_PLLCFGR_PLLQ_Pos);
    RCC->PLLCFGR |=(4<<RCC_PLLCFGR_PLLM_Pos) | (168<<RCC_PLLCFGR_PLLN_Pos) | (4<<RCC_PLLCFGR_PLLQ_Pos) | RCC_PLLCFGR_PLLSRC_HSE;

    RCC->CR |=RCC_CR_PLLON;
    while(!(RCC->CR & RCC_CR_PLLRDY));

    RCC->CFGR |=RCC_CFGR_SW_PLL;
    while((RCC->CFGR & RCC_CFGR_SW)!=RCC_CFGR_SW_PLL);
}

/*static void blink(void *param) {
	(void)param;

	uint8_t state = 0;

	while(1) {
		led_set_green(state);
		//led_set_yellow(!state);

		state = !state;

		vTaskDelay(200);
	}
}*/

int main() {

	NVIC_SetPriorityGrouping(0);
	clock_init();
	uart2_init();
    uart3_init();
	i2c1_init();
	adc_init();
    
    cli_init();
	gui_init();
	motors_init();
	periph_init();
	rc5_init();

	robot_init();

	//xTaskCreate(blink, "blink", 130, NULL, 4, NULL);

    vTaskStartScheduler();

    return 0;
}

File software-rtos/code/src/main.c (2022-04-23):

#include <stdint.h>

#include "stm32f4xx.h"
#include "FreeRTOS.h"
#include "task.h"

#include "config.h"

void greenTask(void *param) {
    (void)param;

    while(1) {
        GPIOB->BSRR |=GPIO_BSRR_BS15;
        vTaskDelay(1000);
        
        GPIOB->BSRR |=GPIO_BSRR_BR15;
        vTaskDelay(1000);
    }
}

void yellowTask(void *param) {
    (void)param;

    while(1) {
        GPIOB->BSRR |=GPIO_BSRR_BS14;
        vTaskDelay(100);
        
        GPIOB->BSRR |=GPIO_BSRR_BR14;
        vTaskDelay(100);
    }
}

int main() {

    NVIC_SetPriorityGrouping(0);

    Clock_Init();

    // PA5
    RCC->AHB1ENR |=RCC_AHB1ENR_GPIOBEN;
    GPIOB->MODER |=GPIO_MODER_MODER15_0 | GPIO_MODER_MODER14_0;;

    xTaskCreate(greenTask, "led green", 1024, NULL, 4, NULL);
    xTaskCreate(yellowTask, "led yellow", 1024, NULL, 4, NULL);

    vTaskStartScheduler();

    return 0;
}

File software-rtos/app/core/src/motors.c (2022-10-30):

#include "motors.h"

static arm_pid_instance_f32 pid[4] = {0};
static float vel_setpoint[4] = {0};
static float vel_curr[4] = {0};
static float pwr_ctrl[4] = {0};
static motors_control_type_t control = MOTORS_CLOSE_LOOP;

static float calculate_vel(const int32_t pos_curr, const int32_t pos_last) {
	const int32_t delta = motors_get_position_delta(pos_last, pos_curr);

	return (float)delta*MOTORS_PID_FREQ/MOTORS_ENCODER_CPR;
}

static float compensate_power(const float input) {
	if(input>=-MOTORS_PWR_COMP_EPS && input<=MOTORS_PWR_COMP_EPS)
		return 0.f;

	if(input>MOTORS_PWR_COMP_EPS) {
		const float a = (MOTORS_PWR_COMP_VAL - 1.f)/(MOTORS_PWR_COMP_EPS - 1.f);
		const float b = (MOTORS_PWR_COMP_EPS - MOTORS_PWR_COMP_VAL)/(MOTORS_PWR_COMP_EPS - 1.f);
		
		return a*input + b;
	}

	const float a = (MOTORS_PWR_COMP_VAL - 1.f)/(MOTORS_PWR_COMP_EPS - 1.f);
	const float b = -(MOTORS_PWR_COMP_EPS - MOTORS_PWR_COMP_VAL)/(MOTORS_PWR_COMP_EPS - 1.f);
	
	return a*input + b;
}

static void update(void *param) {
	(void)param;

	int32_t pos_last[4] = {0};
	int32_t pos_curr[4] = {0};

	motors_set_power(pwr_ctrl);

	while(1) {
		motors_get_position(pos_curr);

		vel_curr[0] = -calculate_vel(pos_curr[0], pos_last[0]);
		vel_curr[1] = calculate_vel(pos_curr[1], pos_last[1]);
		vel_curr[2] = calculate_vel(pos_curr[2], pos_last[2]);
		vel_curr[3] = -calculate_vel(pos_curr[3], pos_last[3]);

		if(control==MOTORS_CLOSE_LOOP) {
			pwr_ctrl[0] = -arm_pid_f32(&pid[0], vel_curr[0] - vel_setpoint[0]);
			pwr_ctrl[1] = -arm_pid_f32(&pid[1], vel_curr[1] - vel_setpoint[1]);
			pwr_ctrl[2] = -arm_pid_f32(&pid[2], vel_curr[2] - vel_setpoint[2]);
			pwr_ctrl[3] = -arm_pid_f32(&pid[3], vel_curr[3] - vel_setpoint[3]);

			motors_set_power(pwr_ctrl);
		}

		memcpy(pos_last, pos_curr, 4*sizeof(int32_t));

		#ifdef MOTOR_DEBUG
			char b[64] = {0};
			snprintf(b, 64, "pos %+ld\t%+ld\t%+ld\t%+ld\n", pos_curr[0], pos_curr[1], pos_curr[2], pos_curr[3]);
			//snprintf(b, 64, "vel %+.2f\t%+.2f\t%+.2f\t%+.2f\n", (double)vel_curr[0], (double)vel_curr[1], (double)vel_curr[2], (double)vel_curr[3]);
			//snprintf(b, 64, "pwr %+.2f\t%+.2f\t%+.2f\t%+.2f\n", (double)pwr[0], (double)pwr[1], (double)pwr[2], (double)pwr[3]);
			uart2_transmit(b, strlen(b));
			uart3_transmit(b, strlen(b));
		#endif

		vTaskDelay(1000/MOTORS_PID_FREQ);
	}
}

void motors_init() {

	for(uint8_t i=0; i<4; i++) {
		pid[i].Kp = MOTORS_PID_KP;
		pid[i].Ki = MOTORS_PID_KI;
		pid[i].Kd = MOTORS_PID_KD;
		arm_pid_init_f32(&pid[i], 1);
	}

	xTaskCreate(update, "pid update", 1024, NULL, 4, NULL);

	// PC6 -> RB IN1
    // PC7 -> RB IN2
	// PC8 -> RF IN1
    // PC9 -> RF IN2
    RCC->AHB1ENR |=RCC_AHB1ENR_GPIOCEN;
    GPIOC->MODER |=(2<<GPIO_MODER_MODE6_Pos) | (2<<GPIO_MODER_MODE7_Pos) | (2<<GPIO_MODER_MODE8_Pos) | (2<<GPIO_MODER_MODE9_Pos);
    GPIOC->AFR[0] |=(3<<GPIO_AFRL_AFSEL6_Pos) | (3<<GPIO_AFRL_AFSEL7_Pos);
	GPIOC->AFR[1] |=(3<<GPIO_AFRH_AFSEL8_Pos) | (3<<GPIO_AFRH_AFSEL9_Pos);

    // TIM8 CH1 -> RB IN1
    // TIM8 CH2 -> RB IN2
	// TIM8 CH3 -> RF IN1
    // TIM8 CH4 -> RF IN2
    RCC->APB2ENR |=RCC_APB2ENR_TIM8EN;
    TIM8->ARR = 1000;
    TIM8->CCMR1 |=(6<<TIM_CCMR1_OC1M_Pos) | (6<<TIM_CCMR1_OC2M_Pos) | TIM_CCMR1_OC1PE | TIM_CCMR1_OC2PE;
	TIM8->CCMR2 |=(6<<TIM_CCMR2_OC3M_Pos) | (6<<TIM_CCMR2_OC4M_Pos) | TIM_CCMR2_OC3PE | TIM_CCMR2_OC4PE;
    TIM8->CCER |=TIM_CCER_CC1E | TIM_CCER_CC2E | TIM_CCER_CC3E | TIM_CCER_CC4E;
    TIM8->BDTR |=TIM_BDTR_MOE;
    TIM8->CR1 |=TIM_CR1_CEN;

	// PA10 -> LF IN1
    // PA11 -> LF IN2
	// PA8  -> LB IN1
    // PA9  -> LB IN2
    RCC->AHB1ENR |=RCC_AHB1ENR_GPIOAEN;
    GPIOA->MODER |=(2<<GPIO_MODER_MODE8_Pos) | (2<<GPIO_MODER_MODE9_Pos) | (2<<GPIO_MODER_MODE10_Pos) | (2<<GPIO_MODER_MODE11_Pos);
	GPIOA->AFR[1] |=(1<<GPIO_AFRH_AFSEL8_Pos) | (1<<GPIO_AFRH_AFSEL9_Pos) | (1<<GPIO_AFRH_AFSEL10_Pos) | (1<<GPIO_AFRH_AFSEL11_Pos);

    // TIM1 CH1 -> LB IN1
    // TIM1 CH2 -> LB IN2
	// TIM1 CH3 -> LF IN1
    // TIM1 CH4 -> LF IN2
    RCC->APB2ENR |=RCC_APB2ENR_TIM1EN;
    TIM1->ARR = 1000;
    TIM1->CCMR1 |=(6<<TIM_CCMR1_OC1M_Pos) | (6<<TIM_CCMR1_OC2M_Pos) | TIM_CCMR1_OC1PE | TIM_CCMR1_OC2PE;
	TIM1->CCMR2 |=(6<<TIM_CCMR2_OC3M_Pos) | (6<<TIM_CCMR2_OC4M_Pos) | TIM_CCMR2_OC3PE | TIM_CCMR2_OC4PE;
    TIM1->CCER |=TIM_CCER_CC1E | TIM_CCER_CC2E | TIM_CCER_CC3E | TIM_CCER_CC4E;
    TIM1->BDTR |=TIM_BDTR_MOE;
    TIM1->CR1 |=TIM_CR1_CEN;

	// PA15 -> LF A
    // PB3  -> LF B
    RCC->AHB1ENR |=RCC_AHB1ENR_GPIOAEN;
	GPIOA->MODER |=(2<<GPIO_MODER_MODE15_Pos);
    GPIOA->AFR[1] |=(1<<GPIO_AFRH_AFSEL15_Pos);

	RCC->AHB1ENR |=RCC_AHB1ENR_GPIOBEN;
    GPIOB->MODER |=(2<<GPIO_MODER_MODE3_Pos);
    GPIOB->AFR[0] |=(1<<GPIO_AFRL_AFSEL3_Pos);

    // TIM2 CH1 -> LF A
    // TIM2 CH2 -> LF B
    RCC->APB1ENR |=RCC_APB1ENR_TIM2EN;
    TIM2->ARR = 65535;
    TIM2->CCMR1 |=(1<<TIM_CCMR1_CC1S_Pos) | (1<<TIM_CCMR1_CC2S_Pos);
    TIM2->SMCR |=(3<<TIM_SMCR_SMS_Pos);
    TIM2->CR1 |=TIM_CR1_CEN;

	// PA0 -> RF A
    // PA1 -> RF B
    RCC->AHB1ENR |=RCC_AHB1ENR_GPIOBEN;
    GPIOB->MODER |=(2<<GPIO_MODER_MODE6_Pos) | (2<<GPIO_MODER_MODE7_Pos);
    GPIOB->AFR[0] |=(2<<GPIO_AFRL_AFSEL6_Pos) | (2<<GPIO_AFRL_AFSEL7_Pos);

    // TIM4 CH1 -> RF A
    // TIM4 CH2 -> RF B
    RCC->APB1ENR |=RCC_APB1ENR_TIM4EN;
    TIM4->ARR = 65535;
    TIM4->CCMR1 |=(1<<TIM_CCMR1_CC1S_Pos) | (1<<TIM_CCMR1_CC2S_Pos);
    TIM4->SMCR |=(3<<TIM_SMCR_SMS_Pos);
    TIM4->CR1 |=TIM_CR1_CEN;

	// PA0 -> RB A
    // PA1 -> RB B
    RCC->AHB1ENR |=RCC_AHB1ENR_GPIOAEN;
    GPIOA->MODER |=(2<<GPIO_MODER_MODE0_Pos) | (2<<GPIO_MODER_MODE1_Pos);
    GPIOA->AFR[0] |=(2<<GPIO_AFRL_AFSEL0_Pos) | (2<<GPIO_AFRL_AFSEL1_Pos);

    // TIM5 CH1 -> RB A
    // TIM5 CH2 -> RB B
    RCC->APB1ENR |=RCC_APB1ENR_TIM5EN;
    TIM5->ARR = 65535;
    TIM5->CCMR1 |=(1<<TIM_CCMR1_CC1S_Pos) | (1<<TIM_CCMR1_CC2S_Pos);
    TIM5->SMCR |=(3<<TIM_SMCR_SMS_Pos);
    TIM5->CR1 |=TIM_CR1_CEN;

	// PB4 -> LB A
    // PB5 -> LB B
    RCC->AHB1ENR |=RCC_AHB1ENR_GPIOBEN;
    GPIOB->MODER |=(2<<GPIO_MODER_MODE4_Pos) | (2<<GPIO_MODER_MODE5_Pos);
    GPIOB->AFR[0] |=(2<<GPIO_AFRL_AFSEL4_Pos) | (2<<GPIO_AFRL_AFSEL5_Pos);

    // TIM3 CH1 -> LB A
    // TIM3 CH2 -> LB B
    RCC->APB1ENR |=RCC_APB1ENR_TIM3EN;
    TIM3->ARR = 65535;
    TIM3->CCMR1 |=(1<<TIM_CCMR1_CC1S_Pos) | (1<<TIM_CCMR1_CC2S_Pos);
    TIM3->SMCR |=(3<<TIM_SMCR_SMS_Pos);
    TIM3->CR1 |=TIM_CR1_CEN;
}

void motors_set_control_type(motors_control_type_t c) {
	control = c;

	arm_pid_reset_f32(&pid[0]);
	arm_pid_reset_f32(&pid[1]);
	arm_pid_reset_f32(&pid[2]);
	arm_pid_reset_f32(&pid[3]);
}
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

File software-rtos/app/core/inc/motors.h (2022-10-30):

#ifndef MOTORS_H
#define MOTORS_H

#include "stm32f4xx.h"
#include "FreeRTOS.h"
#include "task.h"
#include "arm_math.h"

#ifdef MOTOR_DEBUG
	#include "uart2.h"
	#include "uart3.h"
#endif

#define MOTORS_PID_KP			0.1f
#define MOTORS_PID_KI			0.01f
#define MOTORS_PID_KD			0.f
#define MOTORS_PID_FREQ			50		// Hz
#define MOTORS_ENCODER_CPR		360

#define MOTORS_PWR_COMP_EPS		0.01f
#define MOTORS_PWR_COMP_VAL		0.55f

#define MOTORS_WHEEL_READIUS	0.0145f	// m
#define MOTORS_TRACK_WIDTH		0.085f	// m
#define MOTORS_WHEELBASE		0.05f	// m

typedef enum {
	MOTORS_OPEN_LOOP,
	MOTORS_CLOSE_LOOP
} motors_control_type_t;

void motors_init();

void motors_set_control_type(motors_control_type_t);
void motors_set_power(float *);
void motors_set_velocity(float *);
void motors_get_position(int32_t *);
void motors_get_velocity(float *);
void motors_get_power(float *);

int32_t motors_get_position_delta(int32_t, int32_t);

#endif

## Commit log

2021-05-13 old models
    [20NK_3-50CM.ipt, 3M_Nut.ipt, Battery[45x24x21].ipt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]
2021-05-14 Hull raw model
    [BatteryPlate.ipt, HM_Knife_cut.ipt, HullBottom.ipt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]
2021-05-14 top hull and electronics
    [HM_Knife_cut.ipt, HullBottom.ipt, HullMid.ipt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]
2021-06-29 Hull modeling in progress
    [HM_Knife_cut.ipt, HullBottom.ipt, HullMid.ipt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]
2021-06-29 Mid hull corrections and phototransistor
    [HM_Knife_cut.ipt, HullMid.ipt, HullMid_MIR.ipt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]
2021-06-30 Front sensors and hull bolts
    [HullBottom.ipt, HullMid.ipt, HullMid_MIR.ipt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]
2021-07-01 Line sensors mount
    [BatteryPlate.ipt, HullBottom.ipt, Sneak100_Zeta.iam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]
2021-07-01 Wheel dimension fix
    [HullBottom.ipt, HullMid.ipt, HullMid_MIR.ipt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]
2021-07-01 Side sensors
    [HullBottom.ipt, HullMid.ipt, HullMid_MIR.ipt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]
2021-07-02 Side sensors complete
    [HullBottom.ipt, HullTop.ipt, MainModule.iam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]
2021-07-02 Blade bolds
    [HM_Knife_cut.ipt, HullBottom.ipt, QTR1A.iam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]
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2021-07-03 line and proximity sensors schematic
    [interface.sch, lineSennsors.sch, motors.sch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]
2021-07-03 User buttons, leds and uart
    [interface.sch, proximitySensors.sch, sneak100_main_board.sch]
2021-07-04 Gap for motor mount and holes
    [HullBottom.ipt, HullMid.ipt, HullMid_MIR.ipt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]
2021-07-05 Hull small changes
    [BatteryPlate.ipt, HullTop.ipt, Sneak100_Zeta.iam]
2021-07-05 Generating stl files for 3D printing
    [BatteryPlate.stl, HullBottom.ipt, HullBottom.stl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]
2021-07-07 Proximity sensor first test
    [interface.sch, lineSennsors.sch, proximitySensors.sch]
2021-07-08 motors circuit scheme
    [interface.sch, lineSennsors.sch, motors.sch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]
2021-07-08 Add stm32f405 uC scheme
    [controller.sch, interface.sch, lineSennsors.sch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]
2021-07-08 Hardware configuration schematic
    [controller.sch, interface.sch, lineSennsors.sch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]
2021-07-08 Change usb connector footprint
    [interface.sch, sneak100_main_board.kicad_pcb]
2021-07-09 Power section scheme
    [controller.sch, interface.sch, lineSennsors.sch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]
2021-07-14 USB FDU mode
    [controller.sch, interface.sch, lineSennsors.sch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]
2021-07-15 Layout progress
    [controller.sch, interface.sch, motors.sch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]
2021-07-21 Add OLED display
    [HullMid.ipt, HullMid_MIR.ipt, HullTop.ipt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]
2021-07-23 Board interface layout
    [HullTop.ipt, MainModule.iam, MaleHeaderPin_1x3.iam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]
2021-07-24 PCB first full layout
    [20NK_3-50CM.ipt, Battery[45x24x21].ipt, Battery[54x30_5x17_5].ipt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]
2021-07-25 More space in top hull and schematic fix
    [HullBottom.ipt, HullTop.ipt, Sneak100_Zeta.iam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]
2021-07-26 bluetooth en & status connection
    [controller.sch, interface.sch, lineSennsors.sch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]
2021-07-26 First routes on PCB
    [sneak100_main_board.kicad_pcb]
2021-08-02 Add external proximity sensor, erase old from schematic
    [Sneak100_Zeta.iam, controller.sch, interface.sch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]
2021-08-07 Hull with external proximity sensors
    [HullBottom.ipt, HullTop.ipt, MainBoard.ipt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]
2021-08-07 line sensors connectors
    [MainModule.iam, Sneak100_Zeta.iam, controller.sch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]
2021-08-08 power rails routed
    [sneak100_main_board.kicad_pcb]
2021-08-08 Motor signals and interface
    [controller.sch, sneak100_main_board.kicad_pcb]
2021-08-08 Remaining signals from uC
    [controller.sch, sneak100_main_board.kicad_pcb]
2021-08-09 proximity sensors connectors
    [lineSennsors.sch, proximitySensors.sch, sneak100_main_board.kicad_pcb]
2021-08-10 programmer connector, proximity sensors routed
    [controller.sch, sneak100_main_board.kicad_pcb]
2021-08-10 ground fill zones and vias
    [sneak100_main_board.kicad_pcb]
2021-08-11 3.3V power lines
    [sneak100_main_board.kicad_pcb]
2021-08-12 Silk layer text
    [proximitySensors.sch, sneak100_main_board.kicad_pcb]
2021-08-14 Generate gerbers
    [motors.sch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]
2021-08-14 Add thermal gap to motor bridges
    [sneak100_main_board-B_Cu.gbr, sneak100_main_board-B_Mask.gbr, sneak100_main_board-B_Paste.gbr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]
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2021-08-15 motor bridges solid thermal pad
    [sneak100_main_board-B_Cu.gbr, sneak100_main_board-B_Mask.gbr, sneak100_main_board-B_Paste.gbr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]
2021-08-15 component list and values fix
    [controller.sch, interface.sch, power.sch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]
2021-08-16 Bigger tantalum capacitors
    [controller.sch, motors.sch, power.sch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]
2021-08-21 Motors & encoder software fix
    [main.c]
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2021-08-30 Hull smoothing
    [BatteryPlate.ipt, HullBottom.ipt, HullTop.ipt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]
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2021-09-20 Start creation of documentation
    [Sneak100_Zeta.iam, controller.sch, interface.sch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]
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2021-09-28 uController routes in progress
    [controller.sch, sneak100_main_board.kicad_pcb]
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2021-09-29 Version 1.1 probably finished
    [controller.sch, interface.sch, lineSennsors.sch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]
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2021-11-15 gerbers for V1.1 main board
    [Sneak100_Zeta.iam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]
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2021-11-17 update date and title of schematic
    [controller.sch, interface.sch, lineSennsors.sch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]
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2021-12-23 generate schematic V1.1 and fix uart lines directions
    [controller.sch, interface.sch, lineSennsors.sch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]
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2022-01-27 code renovation and bug fixes
    [main.c]
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2022-02-17 CLI error to fix
    [cli.c]
2022-02-20 exception handling and interrupt usage fix
    [cli.c, gui.c, main.c]
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2022-02-26 hull errors fix and test print
    [HullBottom.ipt, HullBottom.stl, HullMid.ipt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]
2022-02-27 3d models fixes
    [BatteryPlate.stl, HM_Knife_cut.ipt, HM_Knife_cut.stl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]
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2022-02-28 line sensors new mount
    [BatteryPlate.ipt, BatteryPlate.stl, HullBottom.ipt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]
2022-03-01 line sensors mount fix
    [HullBottom.ipt, HullBottom.stl, LineSensorPlate.ipt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]
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2022-04-07 Rybnik speedrun: hull with lead
    [HullBottom.ipt, HullBottom.stl, Sneak100_Zeta.iam]
2022-04-08 Rybnik speedrun: robot have correct mass!
    [HullTop.ipt, HullTop.stl]
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2022-04-24 PCB version V2.0 started
    [motors.kicad_sch, perfs.kicad_sch, power.kicad_sch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]
2022-04-24 PCB version 2.0 schematic progress
    [line_board.kicad_sch, motors.kicad_sch, perfs.kicad_sch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]
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2022-04-26 include BOOT1 switch into new PCB
    [ucontroller.kicad_sch]
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2022-04-29 footprints and first layout
    [sneak100_main_board_v2.kicad_pcb, sneak100_main_board_v2.kicad_sch]
2022-05-10 fix cables to proximity sensors
    [cli.c, i2c1.c, main.c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]
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2022-07-20 line sensors quick fix (hardware need to be fix)
    [periph.c]
2022-07-22 revert 3d model changes to current one
    [HullBottom.ipt, IR_TSAL6400.ipt, MainBoard.ipt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]
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2022-07-26 constants fixes and edge-robot angle measurement
    [fight.c, motors.c, motors.h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]
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2022-10-30 Bukareszt speedrun: motor fix
    [motors.c, motors.h]
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
